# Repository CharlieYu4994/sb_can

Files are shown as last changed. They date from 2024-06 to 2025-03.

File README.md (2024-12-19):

# SB_CAN (StealthBurner_CAN)
为 Voron Design 的 StealthBurner 设计的工具头 PCB 板

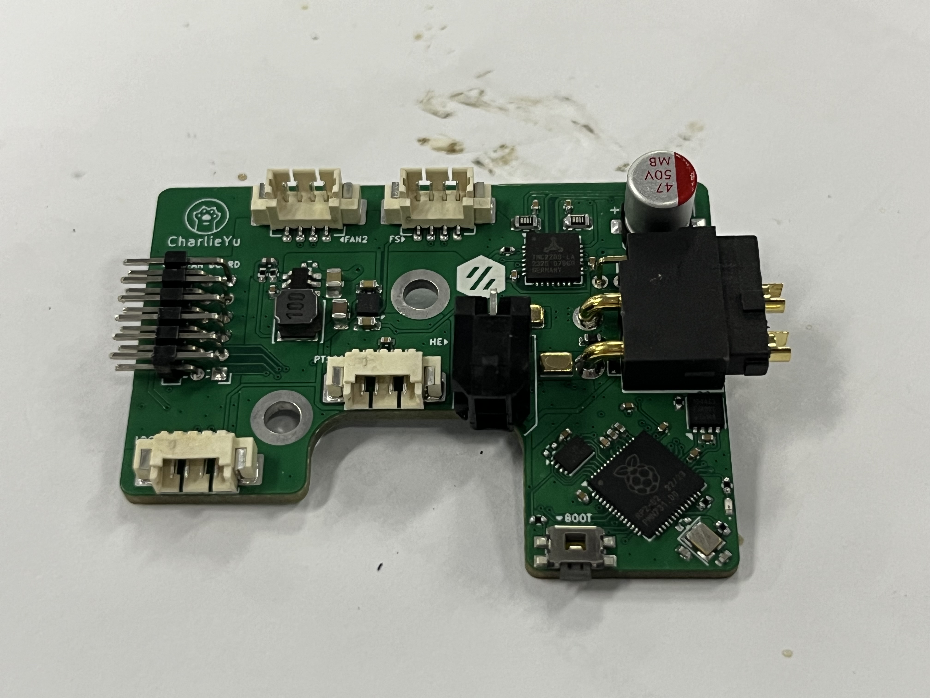
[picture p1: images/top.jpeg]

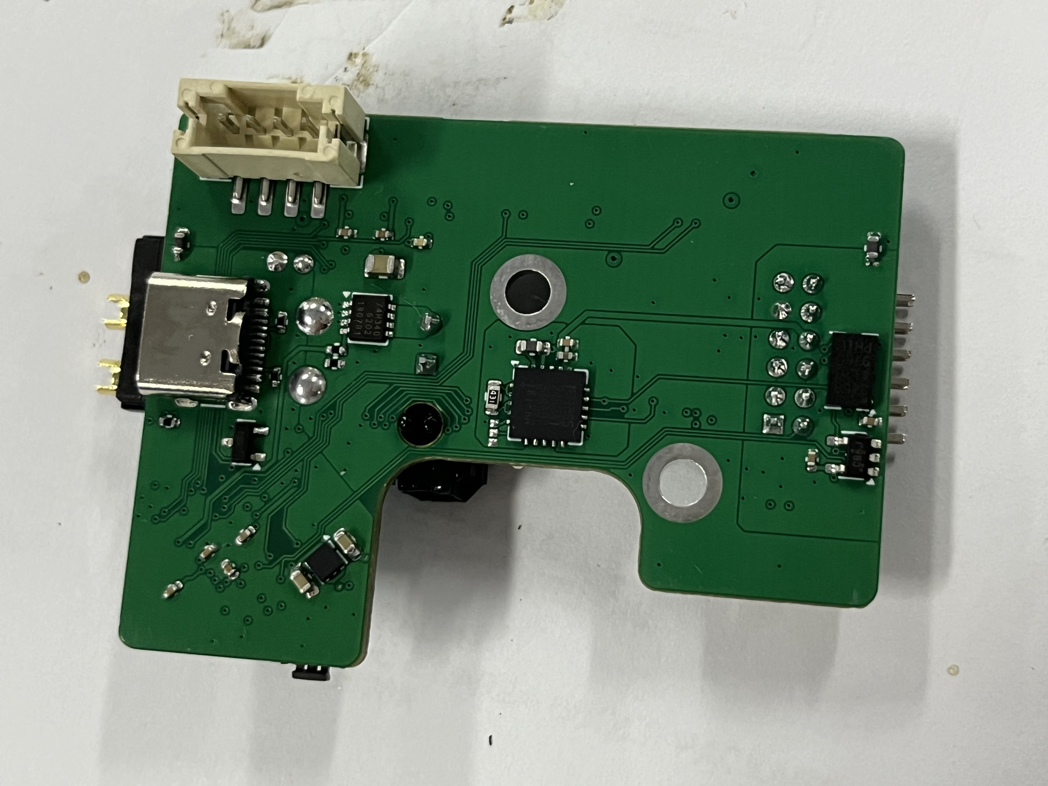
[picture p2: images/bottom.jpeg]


## 特点
+ 使用 StealthBurner 官方的固定孔位，可以无损兼容现有打印件
+ 使用 CAN 总线与主控制器通讯，可靠性更好
+ 板载 ADXL345，无需另外安装加速度计就可以做共振补偿
+ 板载 MAX31865，可以使用二/三/四线制 PT100 温度传感器
+ 板载 TMP235，可以做仓温监控
+ 板载三路四线风扇接口，可以监控风扇转速
+ 预留线性霍尔提供耗材直径检测
+ 预留一路 I2C 接口，可以使用 LDC1612 IDM 传感器

## 使用

### 打样
使用各文件夹内的「SB-**-board.zip」文件即可，建议使用 1.6mm 板厚，4mil 最小线宽

### 接线 (均为从左向右)
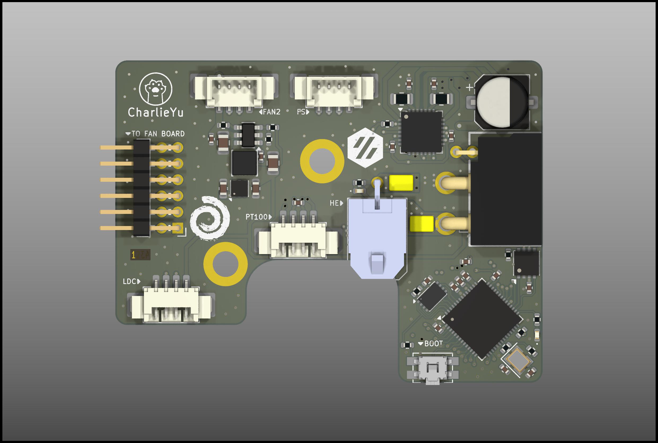
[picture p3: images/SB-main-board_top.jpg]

+ FAN2 (风扇2)
  + +24V
  + GPIO14
  + GPIO15
  + GND
+ FS (耗材传感器)
  + +3.3V
  + GPI16
  + ADC0
  + GND
+ LDC (LDC1612)
  + GND
  + GPIO8
  + GPIO7
  + +5V
+ PT100
  + FORCE-
  + RTDIN-
  + RTDIN+
  + FORCE+
+ HS (上下)
  + GND (GPIO17)
  + +24V

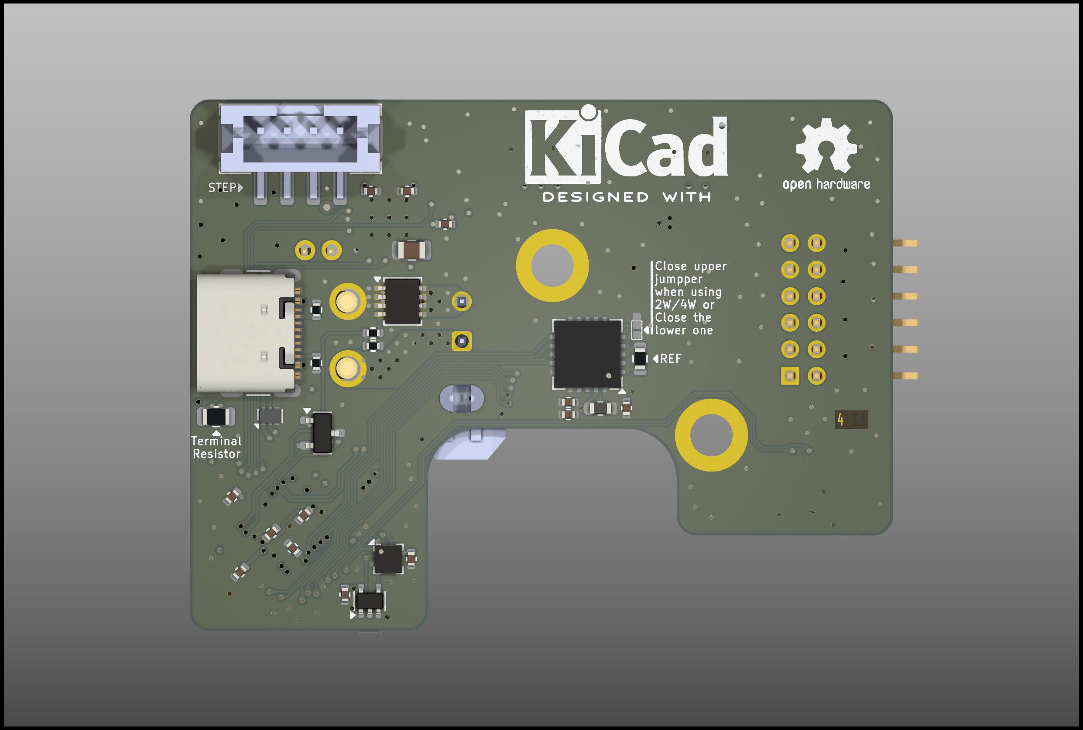
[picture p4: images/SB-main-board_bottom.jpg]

+ STEP (步进电机)
  + A-
  + A+
  + B+
  + B-

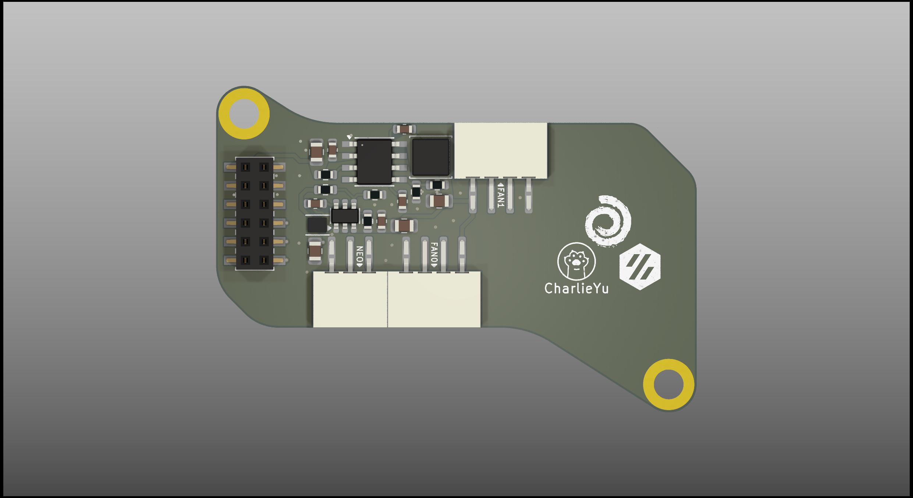
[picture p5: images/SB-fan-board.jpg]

+ FAN1 (风扇1)
  + +12V
  + GPIO13
  + GPIO11
  + GND
+ NEO (WS2812 LED)
  + GND
  + GPIO9
  + +3.7V
+ FAN0 (风扇0)
  + GND
  + GPIO12
  + GPIO10
  + +12V

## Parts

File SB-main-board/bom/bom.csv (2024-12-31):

Reference | Value | Footprint | Qty | DNP
C2,C3 | 15pF | Capacitor_SMD:C_0402_1005Metric | 2
C33 | 10nF | Capacitor_SMD:C_0402_1005Metric | 1
C25 | 22nF | Capacitor_SMD:C_0402_1005Metric | 1
C1,C4,C5,C7,C8,C9,C10,C11,C12,C14,C15,C20,C21,C23,C24,C27,C28,C29,C30,C32,C34,C35,C36 | 100nF | Capacitor_SMD:C_0402_1005Metric | 23
C6,C13,C31 | 1uF | Capacitor_SMD:C_0402_1005Metric | 3
C17 | 1uF | Capacitor_SMD:C_0603_1608Metric | 1
C16 | 2.2uF | Capacitor_SMD:C_1206_3216Metric | 1
C19 | 2.2uF | Capacitor_SMD:C_0603_1608Metric | 1
C26 | 4.7uF | Capacitor_SMD:C_0805_2012Metric | 1
L1 | 10uH | Library:L_Changjiang_FTC303020D | 1
C18 | 22uF | Capacitor_SMD:C_0805_2012Metric | 1
C22 | 100uF | Capacitor_SMD:CP_Elec_6.3x7.7 | 1
R7 | 120R/TBD | Resistor_SMD:R_0805_2012Metric | 1
R15,R16 | 200mR | Resistor_SMD:R_0805_2012Metric | 2
R6 | 430R | Resistor_SMD:R_0402_1005Metric | 1
R17 | 430R | Resistor_SMD:R_0603_1608Metric | 1
R1,R3,R5,R19 | 1K | Resistor_SMD:R_0402_1005Metric | 4
R18 | 2.2K | Resistor_SMD:R_0402_1005Metric | 1
R8,R9 | 5.1K | Resistor_SMD:R_0402_1005Metric | 2
R2 | 10K | Resistor_SMD:R_0402_1005Metric | 1 | DNP (不作装配)
R10,R11,R14,R20 | 10K | Resistor_SMD:R_0402_1005Metric | 4
R13 | 22.1K | Resistor_SMD:R_0402_1005Metric | 1
R12 | 88.7K | Resistor_SMD:R_0402_1005Metric | 1
Y1 | 12MHz | Crystal:Crystal_SMD_2520-4Pin_2.5x2.0mm | 1
FB1 | 120R@100MHz | Inductor_SMD:L_0603_1608Metric | 1
SW1 | BOOT | Library:Panasonic_EVQPUJ_EVQPUA | 1
Q1 | BUK9M4R3-40H | Package_TO_SOT_SMD:LFPAK33 | 1
J2 | Download | Connector_USB:USB_C_Receptacle_GCT_USB4105-xx-A_16P_TopMnt_Horizontal | 1
J3 | Excluder | Library:JST_PH_B4B-PH-SM4-TB_1x04-1MP_P2.00mm_Vertical | 1
J9 | FAN | Library:PinHeader_2x06_P2.00mm_Horizontal | 1
J6 | FAN2 | Library:Molex_PicoBlade_53398-0471_1x04-1MP_P1.25mm_Vertical | 1
J8 | FS | Library:Molex_PicoBlade_53398-0471_1x04-1MP_P1.25mm_Vertical | 1
J5 | Hotend | Library:Molex_Micro-Fit_3.0_43045-0200_2x01_P3.00mm_Horizontal | 1
J7 | LDC | Library:Molex_PicoBlade_53261-0471_1x04-1MP_P1.25mm_Horizontal | 1
D1,D4 | LED | LED_SMD:LED_0402_1005Metric | 2
U8 | LIS2DW12 | Package_LGA:LGA-12_2x2mm_P0.5mm | 1
U10 | LM50 | Package_TO_SOT_SMD:SOT-23 | 1
U5 | LP5912-3.3DRV | Package_SON:WSON-6-1EP_2x2mm_P0.65mm_EP1x1.6mm | 1
U9 | MAX31865xTP | Package_DFN_QFN:TQFN-20-1EP_5x5mm_P0.65mm_EP3.25x3.25mm | 1
R4 | NC | Resistor_SMD:R_0402_1005Metric | 1 | DNP (不作装配)
U7 | OR | Package_TO_SOT_SMD:SOT-353_SC-70-5 | 1
TP1,TP2 | PAD | Library:PAD | 2
J4 | PT100 | Library:Molex_PicoBlade_53261-0471_1x04-1MP_P1.25mm_Horizontal | 1
D3 | RCLAMP0522P | Library:SLP1610P4 | 1
U1 | RP2040 | Package_DFN_QFN:QFN-56-1EP_7x7mm_P0.4mm_EP3.2x3.2mm | 1
D2 | Schottky | Diode_SMD:D_SOD-882D | 1
S1 | Select | Library:Select | 1
U3 | TJA1042TK-3 | Package_DFN_QFN:DFN-8-1EP_3x3mm_P0.65mm_EP1.55x2.4mm | 1
U6 | TMC2209-LA | Package_DFN_QFN:QFN-28-1EP_5x5mm_P0.5mm_EP3.75x3.75mm | 1
U4 | TPS560430YF | Package_TO_SOT_SMD:SOT-23-6 | 1
U2 | W25Q16JVUXIQ | Library:USON-8_2.0x3.0mm_P0.5mm | 1
J1 | XT30PB_IN | Library:AMASS_XT30PW-M_1x02_P2.50mm_Horizontal | 1

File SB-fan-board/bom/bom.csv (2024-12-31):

Reference | Value | Datasheet | Footprint | Qty | DNP
C1,C6,C8 | 100nF | ~ | Capacitor_SMD:C_0603_1608Metric | 3
C2 | 4.7uF | ~ | Capacitor_SMD:C_1206_3216Metric | 1
C3 | 220nF | ~ | Capacitor_SMD:C_0603_1608Metric | 1
C4,C9 | 22uF | ~ | Capacitor_SMD:C_0805_2012Metric | 2
C5 | 1uF | ~ | Capacitor_SMD:C_0603_1608Metric | 1
C7 | 10uF | ~ | Capacitor_SMD:C_0805_2012Metric | 1
J1 | FAN0 | ~ | Library:JST_PH_B4B-PH-K_1x04_P2.00mm_SMD | 1
J2 | FAN1 | ~ | Library:JST_PH_B4B-PH-K_1x04_P2.00mm_SMD | 1
J3 | NEO | ~ | Library:JST_PH_B3B-PH-K_1x03_P2.00mm_SMD | 1
J4 | MAIN | ~ | Library:PinSocket_2x06_P2.00mm_Vertical_SMD | 1
L1 | 10uH | ~ | Inductor_SMD:L_Sunlord_SWPA4030S | 1
L2 | 2.2uH | ~ | Inductor_SMD:L_Murata_DFE201610P | 1
R1,R4,R6 | 10K | ~ | Resistor_SMD:R_0603_1608Metric | 3
R2 | 100K | ~ | Resistor_SMD:R_0603_1608Metric | 1
R3 | 9.09K | ~ | Resistor_SMD:R_0603_1608Metric | 1
R5 | 39K | ~ | Resistor_SMD:R_0603_1608Metric | 1
U1 | LMR33610BDDAR | http://www.ti.com/lit/ds/symlink/lmr33610.pdf | Package_SO:Texas_HSOP-8-1EP_3.9x4.9mm_P1.27mm | 1
U2 | TPS565208 | http://www.ti.com/lit/ds/symlink/tps565208.pdf | Package_TO_SOT_SMD:SOT-23-6 | 1

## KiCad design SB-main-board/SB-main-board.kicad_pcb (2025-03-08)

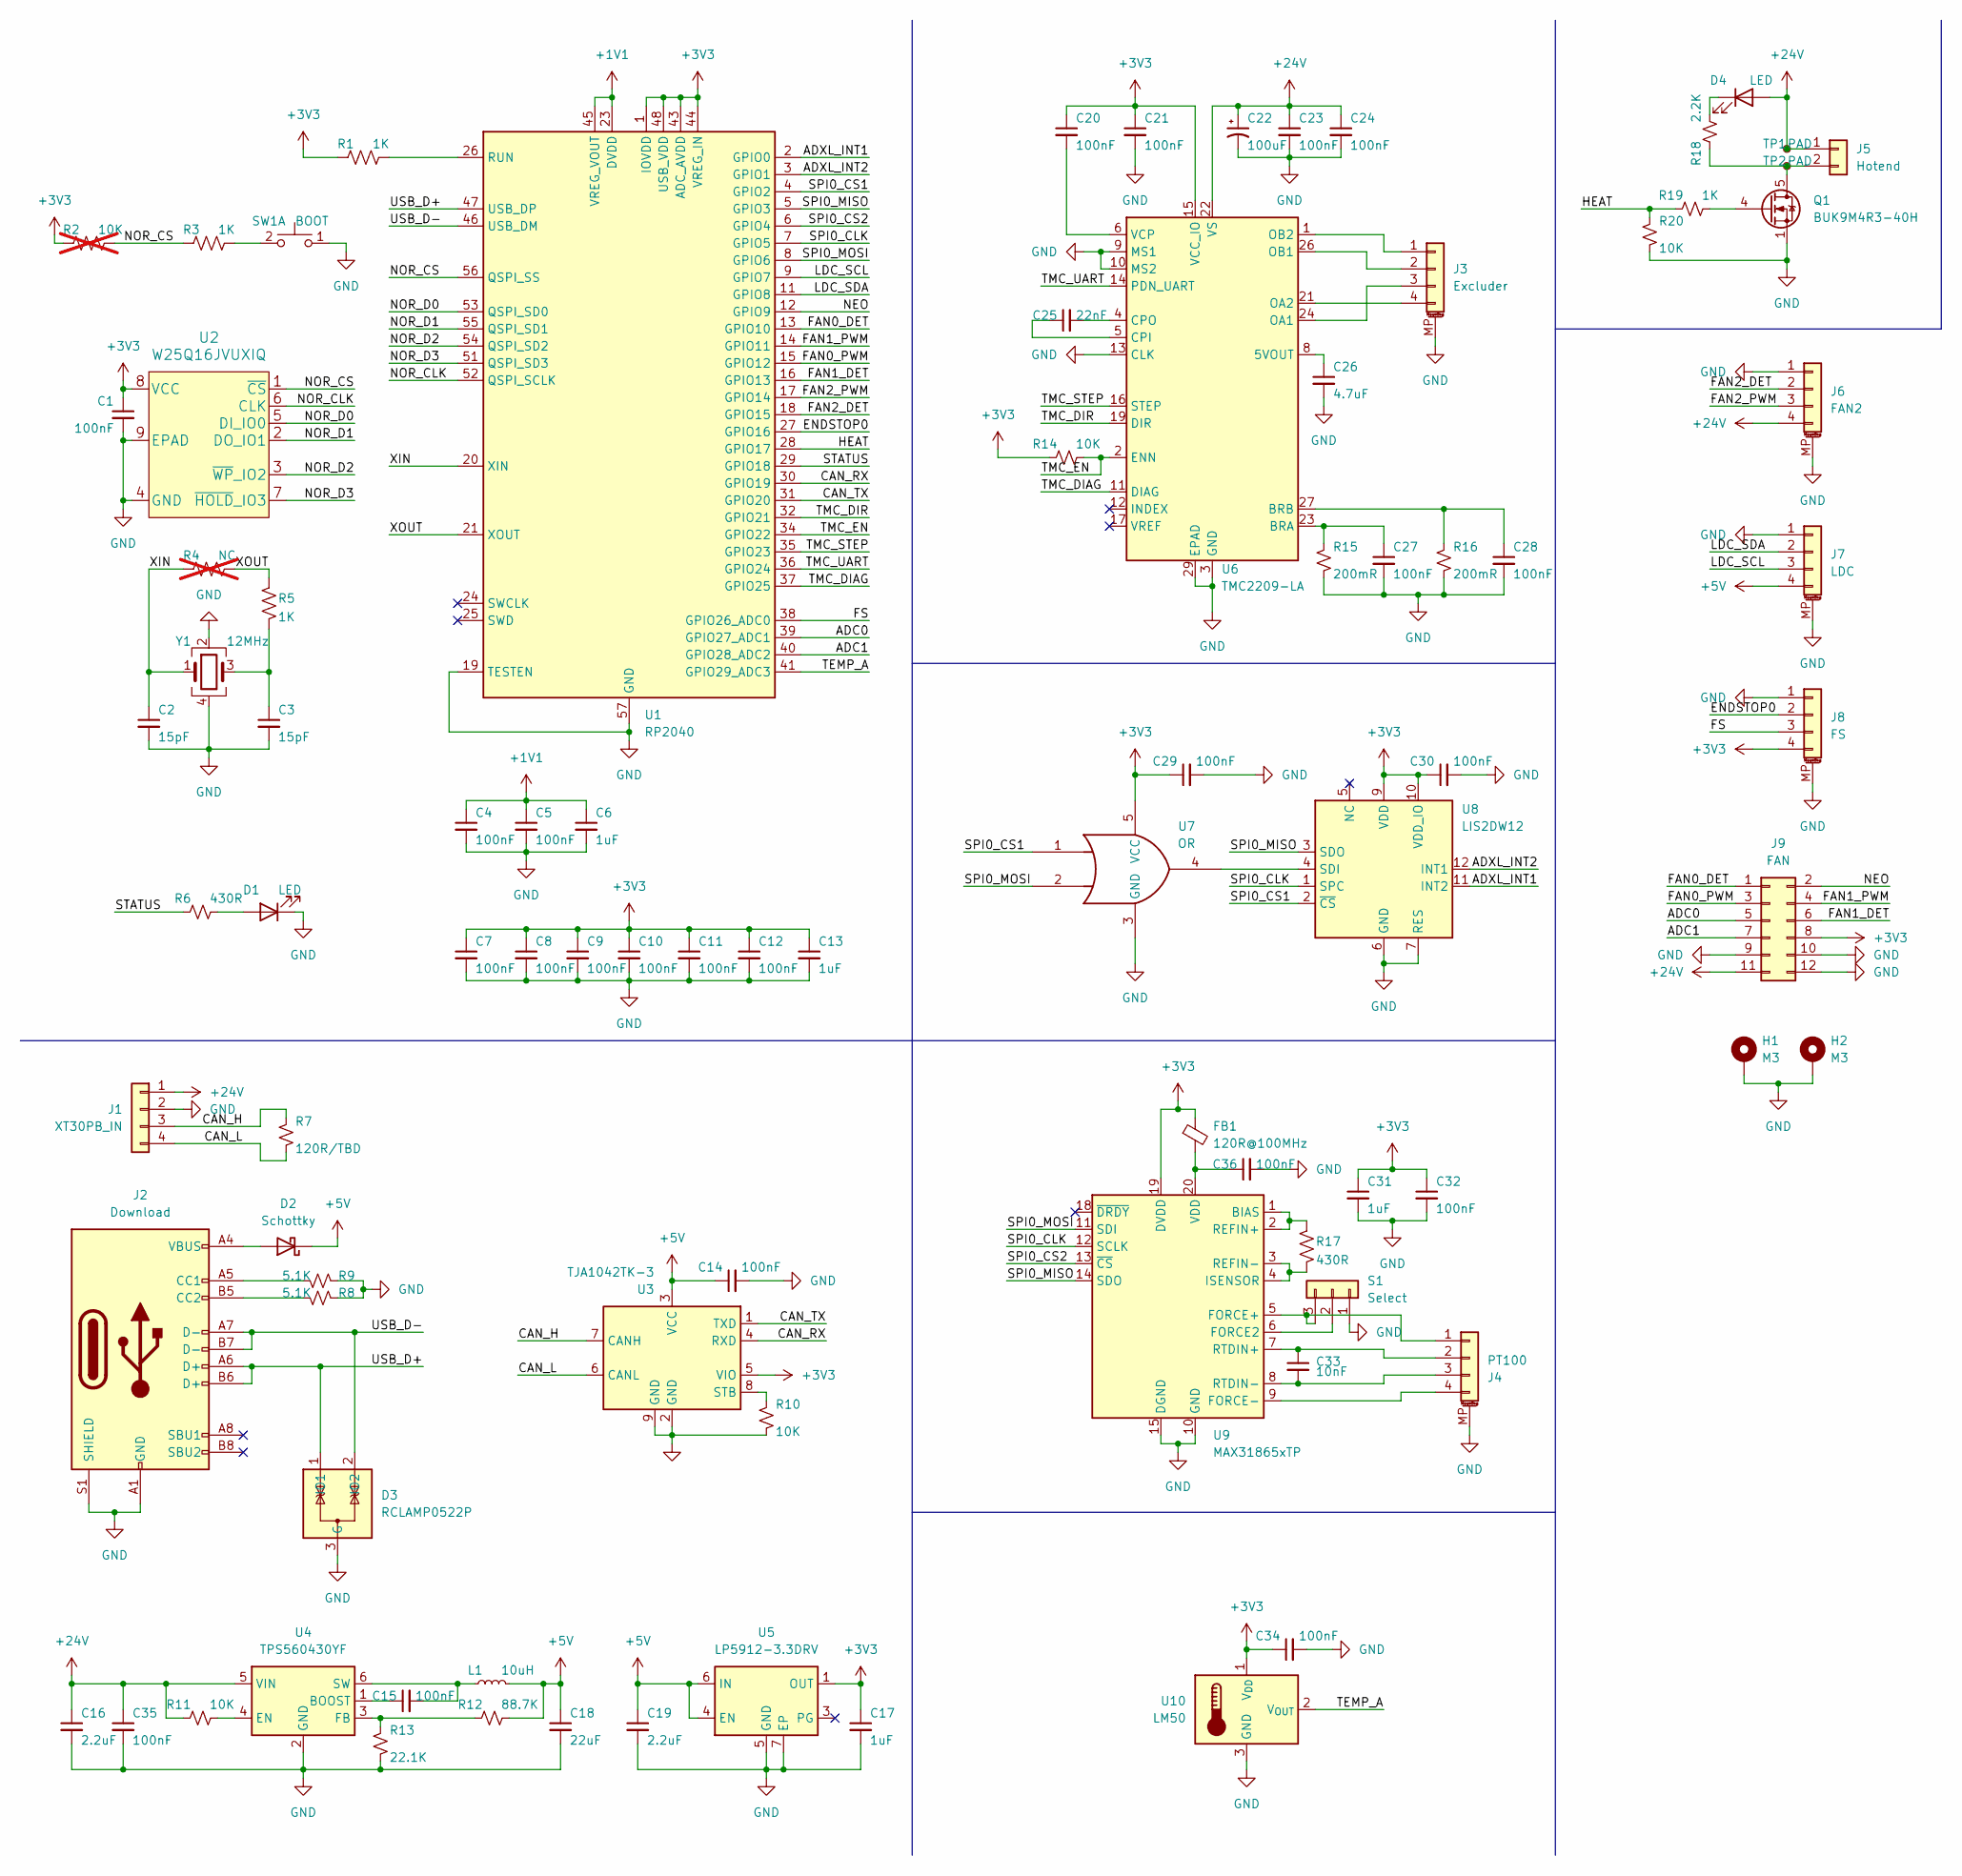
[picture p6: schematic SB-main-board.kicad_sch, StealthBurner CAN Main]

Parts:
C1, C4, C5, C7, C8, C9, C10, C11, C12, C14, C15, C20, C21, C23, C24, C27, C28, C29, C30, C32, C34, C35, C36: 100nF; C_0402_1005Metric
C2, C3: 15pF; C_0402_1005Metric
C6, C13, C31: 1uF; C_0402_1005Metric
C16: 2.2uF; C_1206_3216Metric
C17: 1uF; C_0603_1608Metric
C18: 22uF; C_0805_2012Metric
C19: 2.2uF; C_0603_1608Metric
C22: 100uF; CP_Elec_6.3x7.7
C25: 22nF; C_0402_1005Metric
C26: 4.7uF; C_0805_2012Metric
C33: 10nF; C_0402_1005Metric
D1, D4: LED; LED_0402_1005Metric
D2: Schottky; D_SOD-882D
D3: RCLAMP0522P; SLP1610P4
FB1: 120R@100MHz; L_0603_1608Metric
H1, H2: M3; MountingHole_3.2mm_M3_ISO14580_Pad
J1: XT30PB_IN; AMASS_XT30PW-M_1x02_P2.50mm_Horizontal
J2: Download; USB_C_Receptacle_GCT_USB4105-xx-A_16P_TopMnt_Horizontal
J3: Excluder; JST_PH_B4B-PH-SM4-TB_1x04-1MP_P2.00mm_Vertical
J4: PT100; Molex_PicoBlade_53261-0471_1x04-1MP_P1.25mm_Horizontal
J5: Hotend; Molex_Micro-Fit_3.0_43045-0200_2x01_P3.00mm_Horizontal
J6: FAN2; Molex_PicoBlade_53398-0471_1x04-1MP_P1.25mm_Vertical
J7: LDC; Molex_PicoBlade_53261-0471_1x04-1MP_P1.25mm_Horizontal
J8: FS; Molex_PicoBlade_53398-0471_1x04-1MP_P1.25mm_Vertical
J9: FAN; PinHeader_2x06_P2.00mm_Horizontal
L1: 10uH; L_Changjiang_FTC303020D
Q1: BUK9M4R3-40H; LFPAK33
R1, R3, R5, R19: 1K; R_0402_1005Metric
R2: 10K; R_0402_1005Metric; not fitted
R4: NC; R_0402_1005Metric; not fitted
R6: 430R; R_0402_1005Metric
R7: 120R/TBD; R_0805_2012Metric
R8, R9: 5.1K; R_0402_1005Metric
R10, R11, R14, R20: 10K; R_0402_1005Metric
R12: 88.7K; R_0402_1005Metric
R13: 22.1K; R_0402_1005Metric
R15, R16: 200mR; R_0805_2012Metric
R17: 430R; R_0603_1608Metric
R18: 2.2K; R_0402_1005Metric
S1: Select
SW1: BOOT; Panasonic_EVQPUJ_EVQPUA
TP1, TP2: PAD
U1: RP2040; QFN-56-1EP_7x7mm_P0.4mm_EP3.2x3.2mm
U2: W25Q16JVUXIQ; USON-8_2.0x3.0mm_P0.5mm
U3: TJA1042TK-3; DFN-8-1EP_3x3mm_P0.65mm_EP1.55x2.4mm
U4: TPS560430YF; SOT-23-6
U5: LP5912-3.3DRV; WSON-6-1EP_2x2mm_P0.65mm_EP1x1.6mm
U6: TMC2209-LA; QFN-28-1EP_5x5mm_P0.5mm_EP3.75x3.75mm
U7: OR; SOT-353_SC-70-5
U8: LIS2DW12; LGA-12_2x2mm_P0.5mm
U9: MAX31865xTP; TQFN-20-1EP_5x5mm_P0.65mm_EP3.25x3.25mm
U10: LM50; SOT-23
Y1: 12MHz; Crystal_SMD_2520-4Pin_2.5x2.0mm

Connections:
+1V1: C4.1, C5.1, C6.1, U1.23 (DVDD), U1.45 (VREG_VOUT), U1.50 (DVDD)
+3V3: C1.1, C7.1, C8.1, C9.1, C10.1, C11.1, C12.1, C13.1, C17.1, C20.1, C21.1, C29.1, C30.1, C31.1, C32.1, C34.1, FB1.1, J8.4, J9.8, R1.1, R2.1, R14.1, U1.1 (IOVDD), U1.10 (IOVDD), U1.22 (IOVDD), U1.33 (IOVDD), U1.42 (IOVDD), U1.43 (ADC_AVDD), U1.44 (VREG_IN), U1.48 (USB_VDD), U1.49 (IOVDD), U2.8 (VCC), U3.5 (VIO), U5.1 (OUT), U6.15 (VCC_IO), U7.5 (VCC), U8.9 (VDD), U8.10 (VDD_IO), U9.19 (DVDD), U10.1 (V_{DD})
+5V: C14.1, C18.1, C19.1, D2.1 (K), J7.4, L1.2, R12.2, U3.3 (VCC), U5.4 (EN), U5.6 (IN)
+24V: C16.1, C22.1, C23.1, C24.1, C35.1, D4.2 (A), J1.1, J5.1, J6.4, J9.11, R11.1, TP1.1, U4.5 (VIN), U6.22 (VS), U6.28 (VS)
/ADC0: J9.5, U1.39 (GPIO27_ADC1)
/ADC1: J9.7, U1.40 (GPIO28_ADC2)
/ADXL_INT1: U1.2 (GPIO0), U8.11 (INT2)
/ADXL_INT2: U1.3 (GPIO1), U8.12 (INT1)
/CAN_H: J1.3, R7.1, U3.7 (CANH)
/CAN_L: J1.4, R7.2, U3.6 (CANL)
/CAN_RX: U1.30 (GPIO19), U3.4 (RXD)
/CAN_TX: U1.31 (GPIO20), U3.1 (TXD)
/ENDSTOP0: J8.2, U1.27 (GPIO16)
/FAN0_DET: J9.1, U1.13 (GPIO10)
/FAN0_PWM: J9.3, U1.15 (GPIO12)
/FAN1_DET: J9.6, U1.16 (GPIO13)
/FAN1_PWM: J9.4, U1.14 (GPIO11)
/FAN2_DET: J6.2, U1.18 (GPIO15)
/FAN2_PWM: J6.3, U1.17 (GPIO14)
/FS: J8.3, U1.38 (GPIO26_ADC0)
/HEAT: R19.1, R20.1, U1.28 (GPIO17)
/LDC_SCL: J7.3, U1.9 (GPIO7)
/LDC_SDA: J7.2, U1.11 (GPIO8)
/NEO: J9.2, U1.12 (GPIO9)
/NOR_CLK: U1.52 (QSPI_SCLK), U2.6 (CLK)
/NOR_CS: R2.2, R3.1, U1.56 (QSPI_SS), U2.1 (~CS)
/NOR_D0: U1.53 (QSPI_SD0), U2.5 (DI_IO0)
/NOR_D1: U1.55 (QSPI_SD1), U2.2 (DO_IO1)
/NOR_D2: U1.54 (QSPI_SD2), U2.3 (~WP_IO2)
/NOR_D3: U1.51 (QSPI_SD3), U2.7 (~HOLD_IO3)
/SPI0_CLK: U1.7 (GPIO5), U8.1 (SPC), U9.12 (SCLK)
/SPI0_CS1: U1.4 (GPIO2), U7.1, U8.2 (~CS)
/SPI0_CS2: U1.6 (GPIO4), U9.13 (~CS)
/SPI0_MISO: U1.5 (GPIO3), U8.3 (SDO), U9.14 (SDO)
/SPI0_MOSI: U1.8 (GPIO6), U7.2, U9.11 (SDI)
/STATUS: R6.1, U1.29 (GPIO18)
/TEMP_A: U1.41 (GPIO29_ADC3), U10.2 (V_{OUT})
/TMC_DIAG: U1.37 (GPIO25), U6.11 (DIAG)
/TMC_DIR: U1.32 (GPIO21), U6.19 (DIR)
/TMC_EN: R14.2, U1.34 (GPIO22), U6.2 (ENN)
/TMC_STEP: U1.35 (GPIO23), U6.16 (STEP)
/TMC_UART: U1.36 (GPIO24), U6.14 (PDN_UART)
/USB_D+: D3.1 (IO1), D3.6 (NC), J2.A6 (D+), J2.B6 (D+), U1.47 (USB_DP)
/USB_D-: D3.2 (IO2), D3.5 (NC), J2.A7 (D-), J2.B7 (D-), U1.46 (USB_DM)
/XIN: C2.1, R4.1, U1.20 (XIN), Y1.1
/XOUT: R4.2, R5.2, U1.21 (XOUT)
GND: C1.2, C2.2, C3.2, C4.2, C5.2, C6.2, C7.2, C8.2, C9.2, C10.2, C11.2, C12.2, C13.2, C14.2, C16.2, C17.2, C18.2, C19.2, C21.2, C22.2, C23.2, C24.2, C26.2, C27.2, C28.2, C29.2, C30.2, C31.2, C32.2, C34.2, C35.2, C36.2, D1.1 (K), D3.3 (G), D3.4 (G), H1.1, H2.1, J1.2, J2.A1 (GND), J2.A12 (GND), J2.B1 (GND), J2.B12 (GND), J2.S1 (SHIELD), J3.MP (MountPin), J4.MP (MountPin), J6.1, J6.MP (MountPin), J7.1, J7.MP (MountPin), J8.1, J8.MP (MountPin), J9.9, J9.10, J9.12, Q1.1 (S), Q1.2 (S), Q1.3 (S), R8.1, R9.1, R10.2, R13.2, R15.2, R16.2, R20.2, S1.1, SW1.1 (C), U1.19 (TESTEN), U1.57 (GND), U2.4 (GND), U2.9 (EPAD), U3.2 (GND), U3.9 (GND), U4.2 (GND), U5.5 (GND), U5.7 (EP), U6.3 (GND), U6.9 (MS1), U6.10 (MS2), U6.13 (CLK), U6.18 (GND), U6.29 (EPAD), U7.3 (GND), U8.6 (GND), U8.7 (RES), U8.8 (GND), U9.10 (GND), U9.15 (DGND), U9.16 (GND), U9.21 (GND), U10.3 (GND), Y1.2, Y1.4
unnamed: C3.1, R5.1, Y1.3
unnamed: D1.2 (A), R6.2
unnamed: D2.2 (A), J2.A4 (VBUS), J2.A9 (VBUS), J2.B4 (VBUS), J2.B9 (VBUS)
unnamed: D4.1 (K), R18.2
unnamed: J2.A5 (CC1), R9.2
unnamed: J2.B5 (CC2), R8.2
unnamed: J3.1, U6.1 (OB2)
unnamed: J3.2, U6.26 (OB1)
unnamed: J3.3, U6.24 (OA1)
unnamed: J3.4, U6.21 (OA2)
unnamed: J4.1, S1.3, U9.5 (FORCE+)
unnamed: C33.1, J4.2, U9.7 (RTDIN+)
unnamed: C33.2, J4.3, U9.8 (RTDIN-)
unnamed: J4.4, U9.9 (FORCE-)
unnamed: J5.2, Q1.5 (D), R18.1, TP2.1
unnamed: Q1.4 (G), R19.2
unnamed: S1.2, U9.6 (FORCE2)
unnamed: R3.2, SW1.2 (D)
unnamed: R1.2, U1.26 (RUN)
unnamed: R10.1, U3.8 (STB)
unnamed: C15.1, U4.1 (BOOST)
unnamed: R11.2, U4.4 (EN)
unnamed: R12.1, R13.1, U4.3 (FB)
unnamed: C15.2, L1.1, U4.6 (SW)
unnamed: C26.1, U6.8 (5VOUT)
unnamed: C27.1, R15.1, U6.23 (BRA)
unnamed: C28.1, R16.1, U6.27 (BRB)
unnamed: C25.1, U6.5 (CPI)
unnamed: C25.2, U6.4 (CPO)
unnamed: C20.2, U6.6 (VCP)
unnamed: U7.4, U8.4 (SDI)
unnamed: R17.2, U9.1 (BIAS), U9.2 (REFIN+)
unnamed: R17.1, U9.3 (REFIN-), U9.4 (ISENSOR)
unnamed: C36.1, FB1.2, U9.20 (VDD)

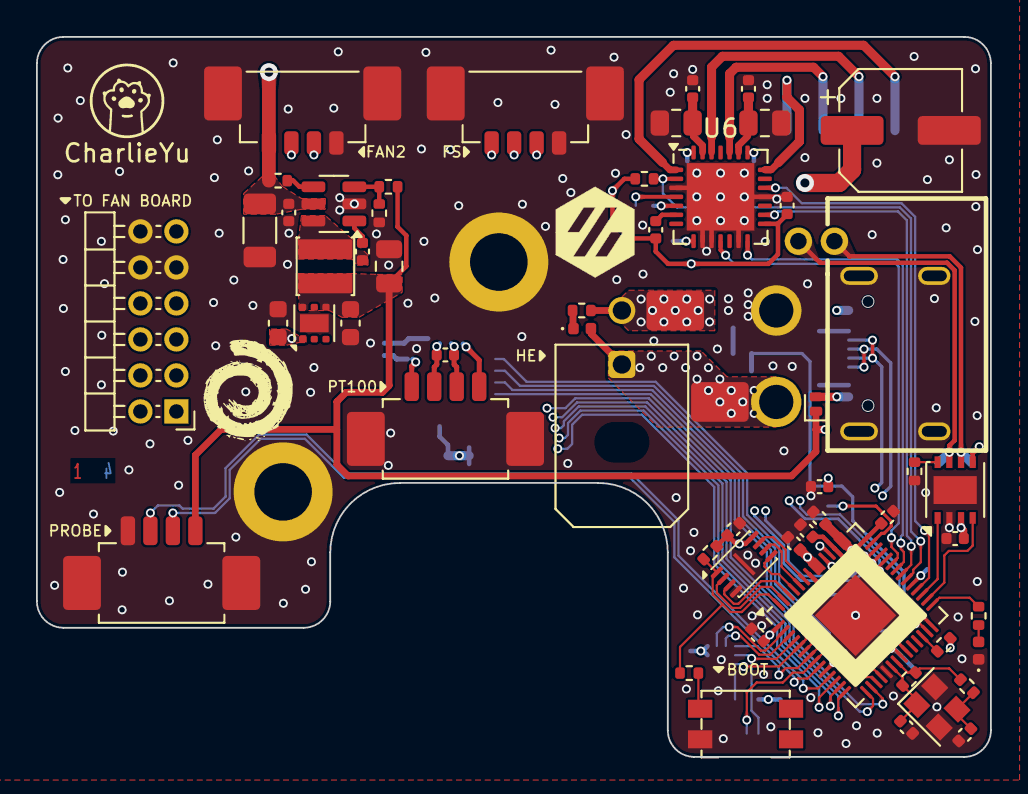
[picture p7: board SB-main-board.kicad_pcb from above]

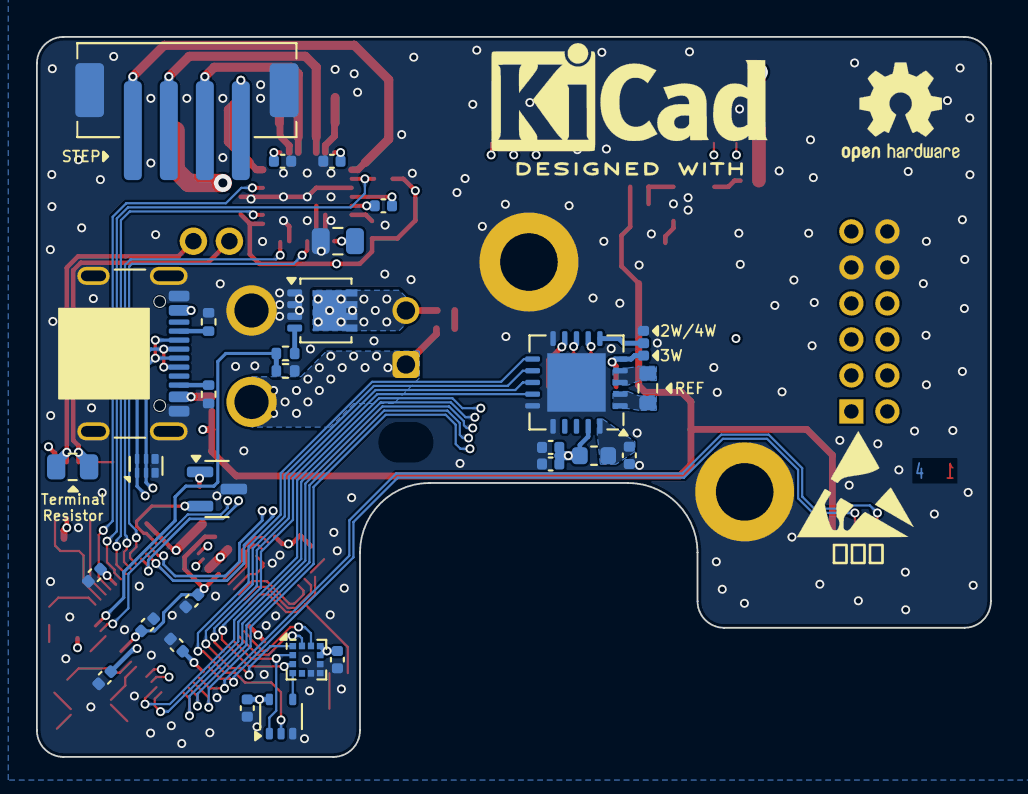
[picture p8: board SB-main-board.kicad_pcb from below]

Board: 4 copper layers, 53.0 x 40.0 mm, 95 parts (33 on the bottom side), 81 nets.

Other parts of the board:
G1: CharlieYu; charlieyu
G2: LOGO; Progynova
G3: Voron Hex; Voron_Logo_Hex
G4: KiCad-Logo2_6mm_SilkScreen
G5: OSHW-Logo2_7.3x6mm_SilkScreen
G6: ESD-Logo_6.6x6mm_SilkScreen

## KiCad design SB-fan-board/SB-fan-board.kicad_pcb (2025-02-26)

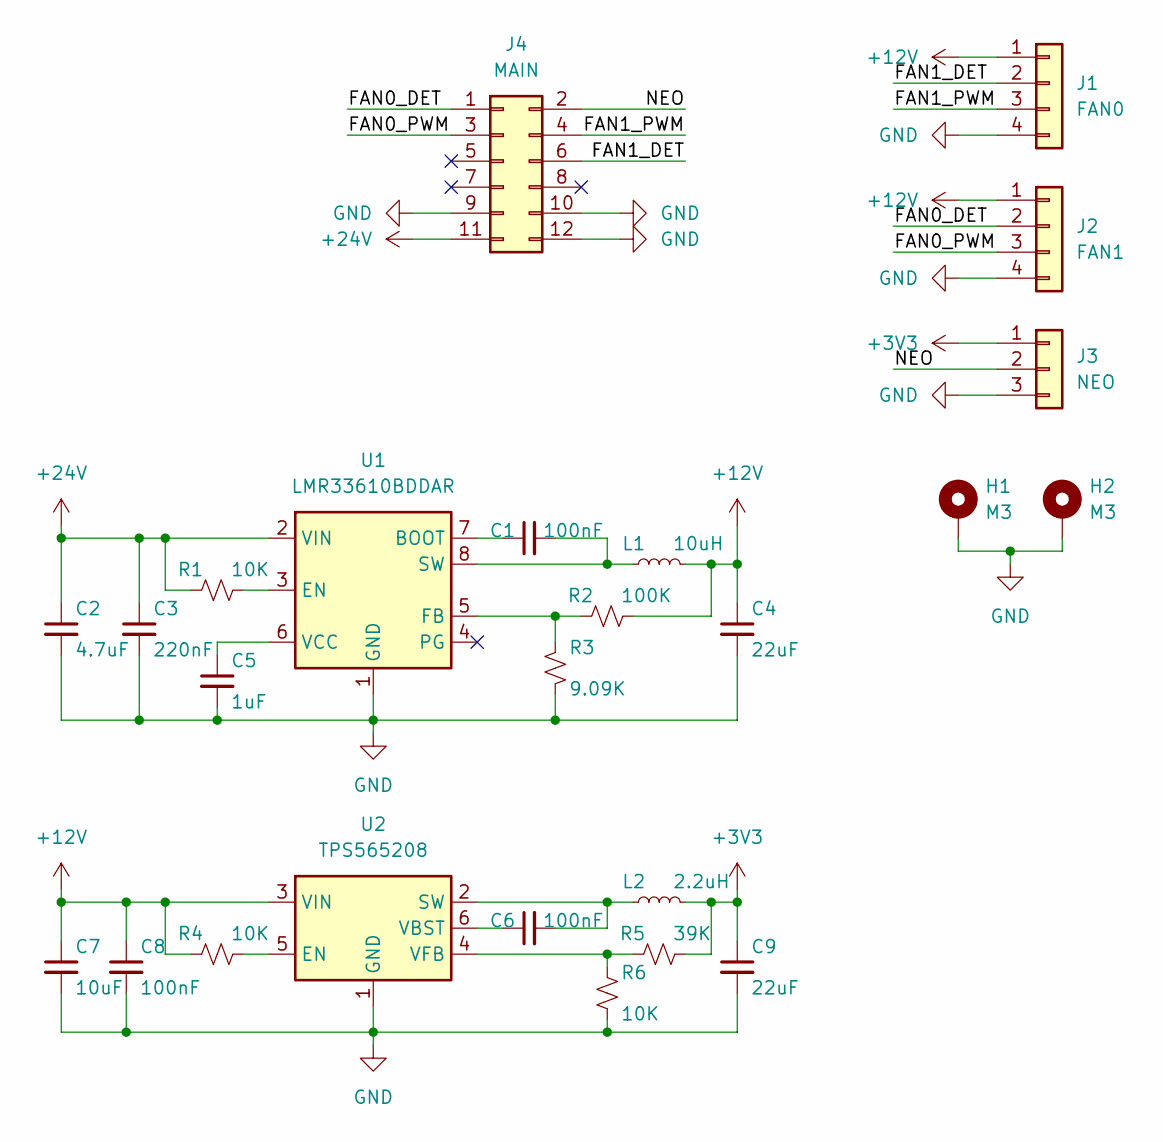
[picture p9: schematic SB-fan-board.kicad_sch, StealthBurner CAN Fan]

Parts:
C1, C6, C8: 100nF; C_0603_1608Metric
C2: 4.7uF; C_1206_3216Metric
C3: 220nF; C_0603_1608Metric
C4, C9: 22uF; C_0805_2012Metric
C5: 1uF; C_0603_1608Metric
C7: 10uF; C_0805_2012Metric
H1, H2: M3; MountingHole_3.2mm_M3_ISO14580_Pad
J1: FAN0; JST_PH_B4B-PH-K_1x04_P2.00mm_SMD
J2: FAN1; JST_PH_B4B-PH-K_1x04_P2.00mm_SMD
J3: NEO; JST_PH_B3B-PH-K_1x03_P2.00mm_SMD
J4: MAIN; PinSocket_2x06_P2.00mm_Vertical_SMD
L1: 10uH; L_Sunlord_SWPA4030S
L2: 2.2uH; L_Murata_DFE201610P
R1, R4, R6: 10K; R_0603_1608Metric
R2: 100K; R_0603_1608Metric
R3: 9.09K; R_0603_1608Metric
R5: 39K; R_0603_1608Metric
U1: LMR33610BDDAR; Texas_HSOP-8-1EP_3.9x4.9mm_P1.27mm
U2: TPS565208; SOT-23-6

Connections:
+3V3: C9.1, J3.1, L2.2, R5.2
+12V: C4.1, C7.1, C8.1, J1.1, J2.1, L1.2, R2.2, R4.1, U2.3 (VIN)
+24V: C2.1, C3.1, J4.11, R1.1, U1.2 (VIN)
/FAN0_DET: J2.2, J4.1
/FAN0_PWM: J2.3, J4.3
/FAN1_DET: J1.2, J4.6
/FAN1_PWM: J1.3, J4.4
/NEO: J3.2, J4.2
GND: C2.2, C3.2, C4.2, C5.2, C7.2, C8.2, C9.2, H1.1, H2.1, J1.4, J2.4, J3.3, J4.9, J4.10, J4.12, R3.2, R6.2, U1.1 (GND), U1.9 (GND), U2.1 (GND)
unnamed: C1.1, U1.7 (BOOT)
unnamed: R1.2, U1.3 (EN)
unnamed: R2.1, R3.1, U1.5 (FB)
unnamed: C1.2, L1.1, U1.8 (SW)
unnamed: C5.1, U1.6 (VCC)
unnamed: R4.2, U2.5 (EN)
unnamed: C6.2, L2.1, U2.2 (SW)
unnamed: C6.1, U2.6 (VBST)
unnamed: R5.1, R6.1, U2.4 (VFB)

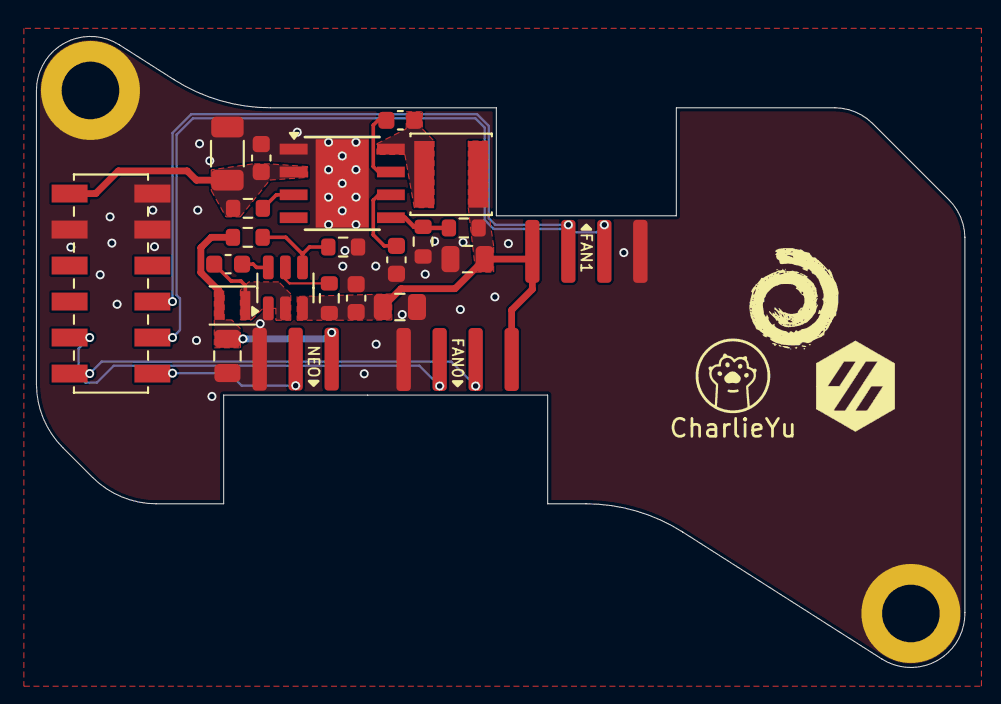
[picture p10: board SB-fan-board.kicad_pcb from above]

Board: 2 copper layers, 51.6 x 35.1 mm, 26 parts (0 on the bottom side), 18 nets.

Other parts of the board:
RFF**: CharlieYu; charlieyu

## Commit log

2024-05-27 Init: initial upload
    [SB_CAN.kicad_pcb, SB_CAN.kicad_sch, connectors.kicad_sch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]
2024-05-27 source: delete unused files
    [connectors.kicad_sch, drivers.kicad_sch, input.kicad_sch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]
2024-05-30 layout: optmise +3v3A power source: use new 3d models
    [SB_CAN.kicad_pcb, SB_CAN.kicad_sch]
2024-05-30 source: move files
    [SB_CAN_MAIN.kicad_pcb, SB_CAN_MAIN.kicad_sch]
2024-05-30 layout: add fan board
    [SB_CAN_FAN.kicad_pcb, SB_CAN_FAN.kicad_sch, SB_CAN_MAIN.kicad_pcb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]
2024-05-31 sch: fix bug that the tja1044 can only use 5V power
    [SB_CAN_MAIN.kicad_pcb, SB_CAN_MAIN.kicad_sch]
2024-05-31 source: rename the pcbs
    [SB-fan-board.kicad_pcb, SB-fan-board.kicad_sch, SB-main-board.kicad_pcb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]
2024-05-31 mechanical: fix interference
    [SB-fan-board.step, SB-main-board.kicad_pcb, SB-main-board.kicad_sch]
2024-05-31 mechanical: optimise installation
    [SB-fan-board.kicad_pcb, SB-main-board.kicad_pcb]
2024-06-01 silkscreen: optmise silkscreen
    [SB-main-board.kicad_pcb, SB-main-board.kicad_sch]
2024-06-01 bugfix: use 5V for IDM sensor
    [SB-main-board.kicad_pcb, SB-main-board.kicad_sch]
2024-06-01 fab: generate gerbers and bom
    [SB-main-board-B_Cu.gbr, SB-main-board-B_Mask.gbr, SB-main-board-B_Paste.gbr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]
2024-06-15 generate gerber files
    [SB-fan-board-B_Cu.gbr, SB-fan-board-B_Mask.gbr, SB-fan-board-B_Paste.gbr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]
2024-06-19 layout: optimise trace
    [SB-main-board.kicad_pcb]
2024-06-23 silkscreen: add more information
    [SB-main-board.kicad_pcb, SB-main-board.kicad_sch]
2024-06-25 sch: optimize return path
    [SB-main-board.kicad_pcb, SB-main-board.kicad_sch]
2024-06-25 fab: regenerate gerbers
    [SB-main-board-B_Cu.gbr, SB-main-board-B_Mask.gbr, SB-main-board-B_Paste.gbr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]
2024-06-25 source: mask is now in gerber folder
2024-06-25 silkscreen: make silkscreen easy to read
    [SB-main-board.kicad_pcb]
2024-07-11 layout: optmise power layout
    [SB-main-board.kicad_pcb, SB-main-board.kicad_sch]
2024-12-10 update to v2
    [SB-main-board.kicad_pcb, SB-main-board.kicad_sch]
2024-12-10 3d: add more 3d modules
    [SB-main-board.kicad_pcb]
2024-12-11 sch: change accelerometer to LIS2DW12
    [SB-main-board.kicad_sch]
2024-12-11 layout: change the accelerometer
    [SB-main-board.kicad_pcb]
2024-12-11 layout: optmise routes
    [SB-main-board.kicad_pcb]
2024-12-11 update fan board to v2
    [SB-fan-board.kicad_pcb, SB-fan-board.kicad_sch]
2024-12-12 generate manufacture files
    [SB-fan-board-B_Cu.gbr, SB-fan-board-B_Mask.gbr, SB-fan-board-B_Paste.gbr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]
2024-12-12 footprint: change the Micro-Fit 3.0 connector
    [SB-main-board.kicad_pcb]
2024-12-12 silkscreen: add silkscreen
    [SB-fan-board.kicad_pcb]
2024-12-12 regenerate manufacture files
    [SB-fan-board-B_Cu.gbr, SB-fan-board-B_Mask.gbr, SB-fan-board-B_Paste.gbr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]
2024-12-12 sch: change the tvs to 0522
    [SB-main-board.kicad_sch]
2024-12-12 layout: change the tvs to 0522
    [SB-main-board-B_Cu.gbr, SB-main-board-B_Mask.gbr, SB-main-board-B_Paste.gbr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]
2024-12-15 change bom
    [SB-fan-board.kicad_pcb, SB-main-board.kicad_pcb, SB-main-board.kicad_sch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]
2024-12-17 layout: delete unused area
    [SB-main-board.kicad_pcb]
2024-12-18 generate latest manufacture files
    [SB-fan-board-B_Cu.gbr, SB-fan-board-B_Mask.gbr, SB-fan-board-B_Paste.gbr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]
2024-12-19 layout: swap the led and the resistor
    [SB-main-board.kicad_pcb, SB-main-board.kicad_sch]
2024-12-19 layout: optime the routes for TMC2209
    [SB-main-board.kicad_pcb]
2024-12-19 3d: add missing module
    [SB-fan-board.kicad_pcb, SB-fan-board.step]
2024-12-20 footprint: change input cap to 1206
    [SB-fan-board.kicad_pcb, SB-fan-board.kicad_sch, SB-main-board.kicad_pcb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]
2024-12-31 layout: optmise layout silkscreen: change silkscreen
    [SB-main-board.kicad_pcb]
2024-12-31 misc: fix typo
    [SB-main-board.kicad_pcb, SB-main-board.kicad_sch, bom.csv]
2024-12-31 misc: update bom
2025-01-01 layout: add rounded pcb
    [SB-main-board-rounded.kicad_pcb]
2025-02-23 misc: update to kicad 9
    [SB-fan-board.kicad_pcb, SB-fan-board.kicad_sch, SB-main-board-rounded.kicad_pcb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]
2025-02-23 misc: delete gerber
    [SB-fan-board-B_Cu.gbr, SB-fan-board-B_Mask.gbr, SB-fan-board-B_Paste.gbr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]
2025-02-23 action: fix kicad_cli error
2025-02-26 misc: update all files to kicad 9
    [SB-fan-board.kicad_pcb, SB-fan-board.kicad_sch, SB-main-board.kicad_pcb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]
2025-02-27 layout: update zone fills
    [SB-main-board.kicad_pcb]
2025-02-27 layout: change zone fill priority
    [SB-main-board.kicad_pcb]
2025-03-08 layout: add teardrops
    [SB-main-board.kicad_pcb]
